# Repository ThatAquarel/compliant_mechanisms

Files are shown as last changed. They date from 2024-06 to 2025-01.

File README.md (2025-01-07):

# Bending Robotic Arm

Built on compliant mechanisms, and handed shearing auxetics. Achieved a snake-like, organic movement. An optical positioning feedback loop completes the control system. The hardware interface is governed by Arduino.

Icons

### Achieved Flexibility
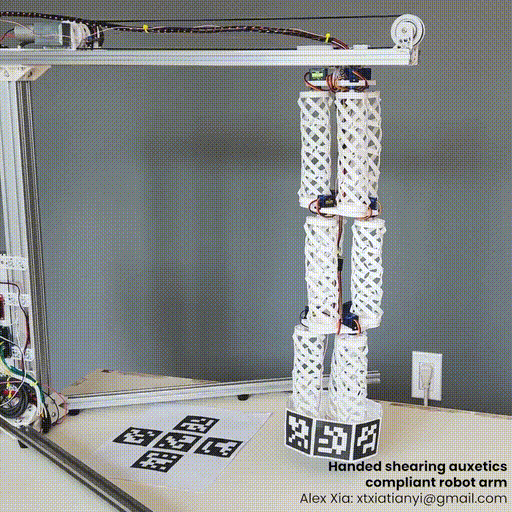
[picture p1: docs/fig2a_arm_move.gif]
Arm Bending Move


### Movement Range
Arm Movement Range

## Author

Alex Xia, personal project. June-December 2024.

## Mechanism of Action

3D-printed, flexible muscles arrayed in sets of three, and stacked together allow for the movement range of the robotic arm. Parallelogram lattices are mapped onto the side surface of a cylinder of ID `38.4mm`. An axial twisting torque extends and contracts the muscle.

### Single Muscle Extension and Contraction

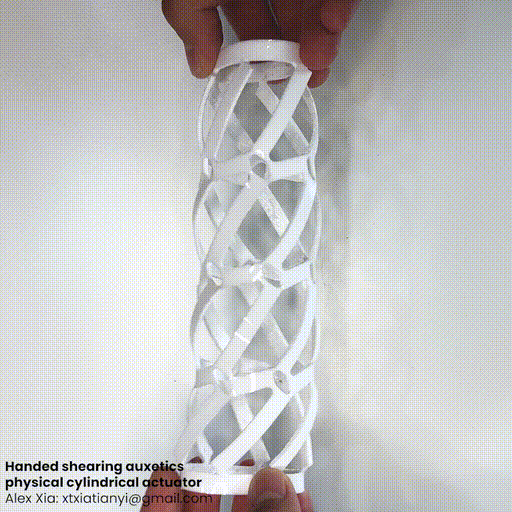
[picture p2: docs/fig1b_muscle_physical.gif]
Muscle Extension and Contraction by Hand


### Muscle Simulation, Blender
Muscle Simulation

## The Concept

Unlike traditional robotic arms, which pivot rigidly around bearings, the compliant muscles allow this arm to bend and twist upon itself, making this special, in my eyes. The snake-like organic movements contrast with the elbowing motion of assembly-line robots, for instance. 

The soft plastics of which the muscles are composed grant safety and simplicity to the design: there are no heavy metal parts moving – which eases assembly – and few differing components (only light servo motors, wiring, and plastic parts).

I see further iterations of this prototype interacting with humans, in palliative care, for example, and for microscopic manipulation.

## How it Works

3D-printed, flexible, cylindrical muscles which contract and extend upon an axial twisting force are arrayed in sets of three, and then layered – achieving a smooth, flexing motion of the whole structure: a flexible and compliant robotic arm.

Each muscle consists of a matrix of parallelograms – which can be sheared into rectangles, achieving extension – mapped and curved onto the surface of a cylinder. 

9 servo motors individually apply torque on each of the muscles to attain a specific pose, which the target is confirmed by an optical positioning system (see Project 2).

This visual positioning data, indeed, completes the feedback loop. A Python script minimizes the distance between the achieved and desired pose, and relays the motor positions to the hardware-controlling Arduino using serial communication. The achieved kinematics resemble that of three stacked Stewart platforms.

## Codebase

- `shearing_auxetics/`: Auxetic materials research and prototypes of muscles
    - `openscad/`: V1: Mesh generation with OpenSCAD.
    - `blender/`: V2: Mesh generation with Python and Blender - final working version of muscles.
    - `render/`: Rendering of V2.
    - `simulation/`: Simulation of edges of V2.

- `arm/`: Implementation of shearing auxetics for the bending arm
    - `hardware/arm_interface`: Serial interface between computer and hardware with Arduino on PlatformIO 
    - `software/`: Control loop on Python
        - `drafts/`: Python control of robotic arm with GUI
            - `optical_positioning_optimize_center.py`: Nelder-mead optimisation to arm position.
            - `optical_positioning_optimize_center_manual.py`: Manual slider-control of robotic arm.
        - `mit/`: Interpolated move examples for MIT Maker Portfolio from recorded positions.

- `optical_positioning/`: Optical positioning for motion tracking and control loop feedback
    - `optical_positioning/`: Optical positioning Python package root.
    - `b_calibrate/`: Cached calibration images.
    - `c_calibrate_matrix/`: Cached calibration matrices.
    - `drafts/`: Testing code for iterative developement.

## Contact

- [Tian Yi, "Alex", Xia](https://github.com/ThatAquarel), xtxiatianyi@gmail.com: 

## References

- Compliant Mechanisms (Howell, 2001).
- Handedness in Shearing Auxetics Creates Rigid and Compliant Structures (Lipton et al., 2018).

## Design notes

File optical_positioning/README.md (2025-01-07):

# Optical Positioning System

Three fisheye cameras locate ArUco markers within their field of view, and transform their perspectives into 3D positions.

Icons

### Custom 3D Motion Capture Software

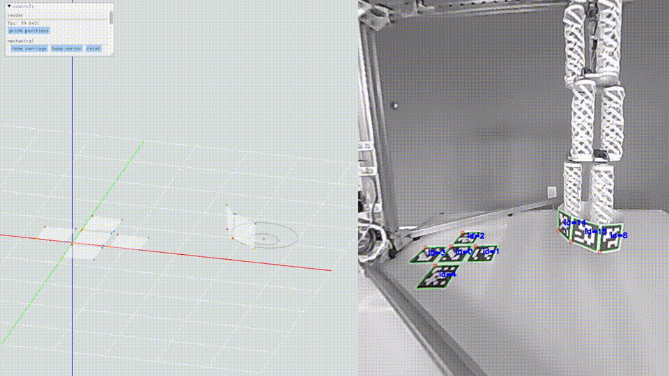
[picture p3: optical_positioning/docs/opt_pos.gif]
3D Motion Capture


### Marker Tracking

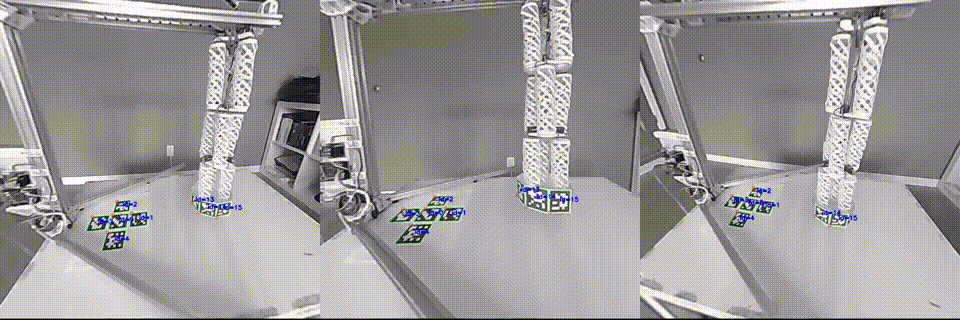
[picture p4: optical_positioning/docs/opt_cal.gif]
ArUco Marker Capture


### Camera Views

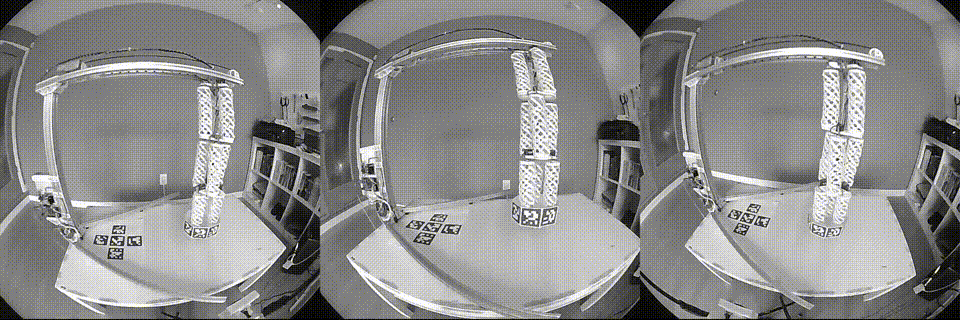
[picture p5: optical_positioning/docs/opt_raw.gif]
Fisheye Camera Views


## Author

Alex Xia, personal project. June-December 2024.

## Computer Vision Principles

The 3D-printed mounts for each of the cameras is my own design. The optical positioning pipeline, along with the feedback loop for my robotic arm, is also my own work built on open-source packages. OpenCV handled the ArUco marker generation and detection, and provided helper functions for calibrating the cameras, and solving for perspective, for example. However, making these preexisting tools work together reliably and fast was my responsibility. Most notably, the linear algebra to match the perspectives of the cameras to each other (the bulk of the computation) is my work, as optimizing my code for up to 120 frames per second required multithreading math.

The theory that backed this implementation was found in research papers and online articles which detailed the Perspective-n-Point problem, and OpenCV’s documentation. Dr. Anton's "Elementary Linear Algebra" also came in handy.

## Design Goals

In building my flexible robotic arm, I realized I needed a reliable positioning system for feedback. I knew that optical was the way to go, but due to the high price point of commercial options, I built my own for cheap, open-sourced it – all while serving as a learning experience for math. 

Currently, the cameras are fixed in place, while objects within their fields of view move: perfect for motion capture in robotics. A similar algorithm holds true if the cameras move, instead, which is my next goal. The cameras can then be placed on the end effector (or achieve the same perspective by the mediation of fiber optic cables) – a necessary field of view if we’re talking about surgery: a possible application for miniaturized flexible robotic arms. This extension of my positioning system is my current goal.

## How it Works

After researching the extravagant pricing options of OptiTrack, I bought three USB fisheye cameras with a 180deg lens for around 100$, and 3D-printed mounts to bolt onto cymbal stands I borrowed from my drum set.

I first calibrated each of the cameras, acquiring their projection and distortion matrices, with different pictures of a known-size checkerboard pattern. The image distorted by the fisheye lens can be undistorted using these matrices, making lines appear straight in-frame. This is crucial as the ArUco marker corner detection would not work otherwise.

Using a known cross pattern, I computed the relative transformation matrices between each camera using OpenCV’s Perspective-n-Point solver. The absolute position with respect to the cross pattern can be therefore determined for each subsequent marker that appears in at least two of the cameras.

## Requirements

- glfw==2.7.0
- imgui==2.0.0
- matplotlib==3.10.0
- numpy==2.2.1
- opencv_python==4.10.0.84
- PyOpenGL==3.1.7
- PyOpenGL==3.1.7
- scipy==1.15.0
- setuptools==69.5.1

## Codebase

- `optical_positioning/`: Optical positioning for motion tracking and control loop feedback
    - `optical_positioning/`: Optical positioning Python package root.
        - `a_constants.py`: Program constants: number of cameras, reference frame ArUco marker placements.
        - `b_calibrate.py`: Take calibration pictures.
        - `c_calibrate_matrix.py`: Fisheye camera calibration and distortion matrix acquisition.
        - `d_compute_pose.py`: 3D pose computation of detected markers from 3 perspectives.
        - `e_render.py`: OpenGL-based custom rendering engine for motion tracking.

    - `b_calibrate/`: Cached calibration images.
    - `c_calibrate_matrix/`: Cached calibration matrices.
    - `drafts/`: Testing code for iterative developement.

## Contact

- [Tian Yi, "Alex", Xia](https://github.com/ThatAquarel), xtxiatianyi@gmail.com:

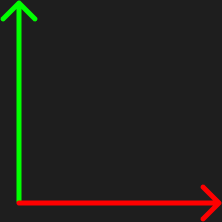
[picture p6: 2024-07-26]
optical_positioning/drafts/aruco/xy_arrows.png

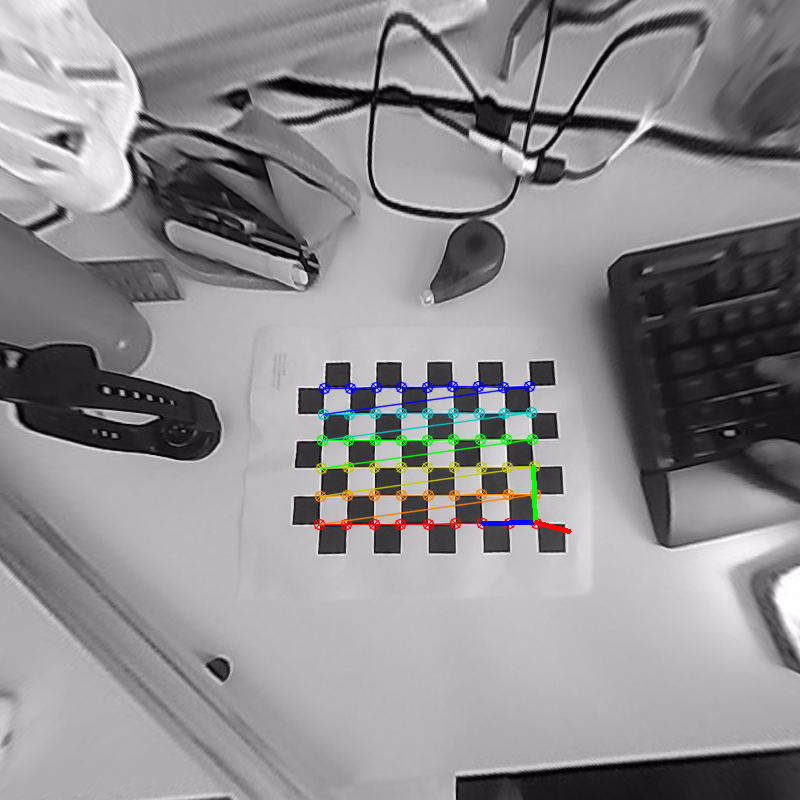
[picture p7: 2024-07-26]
optical_positioning/drafts/raw_compute/img_1_pose.png

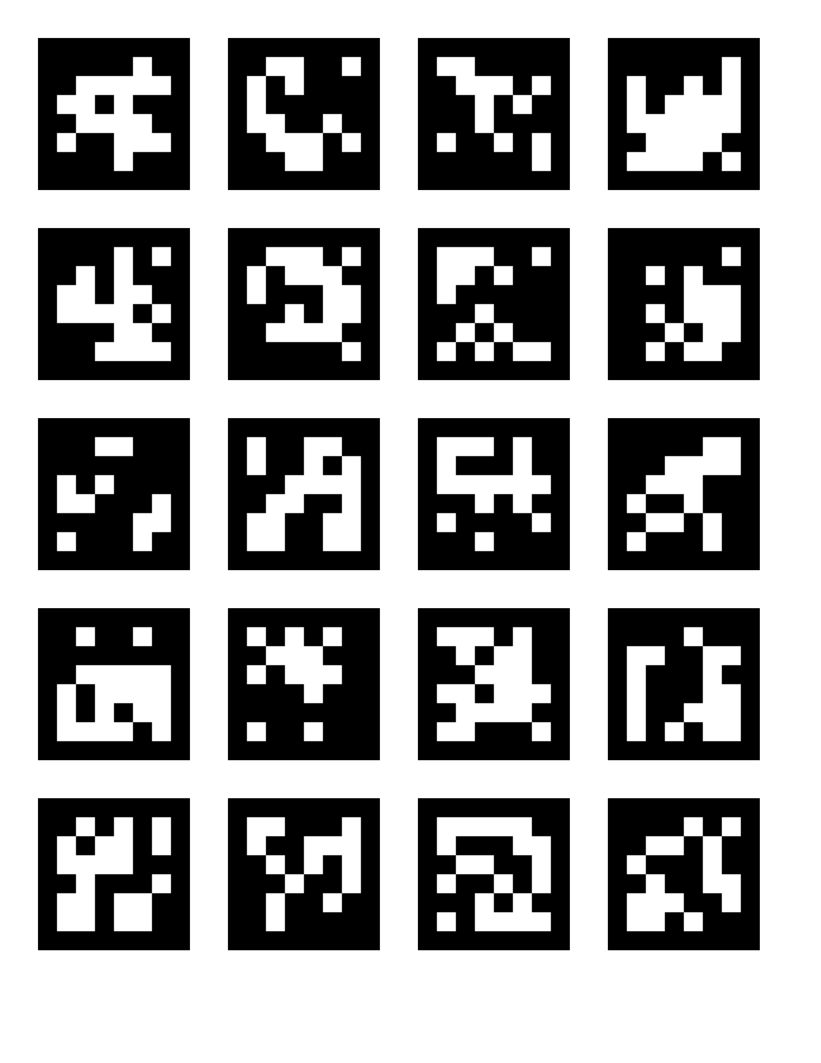
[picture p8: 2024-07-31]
optical_positioning/drafts/aruco/generate_ngrid_4cm.png

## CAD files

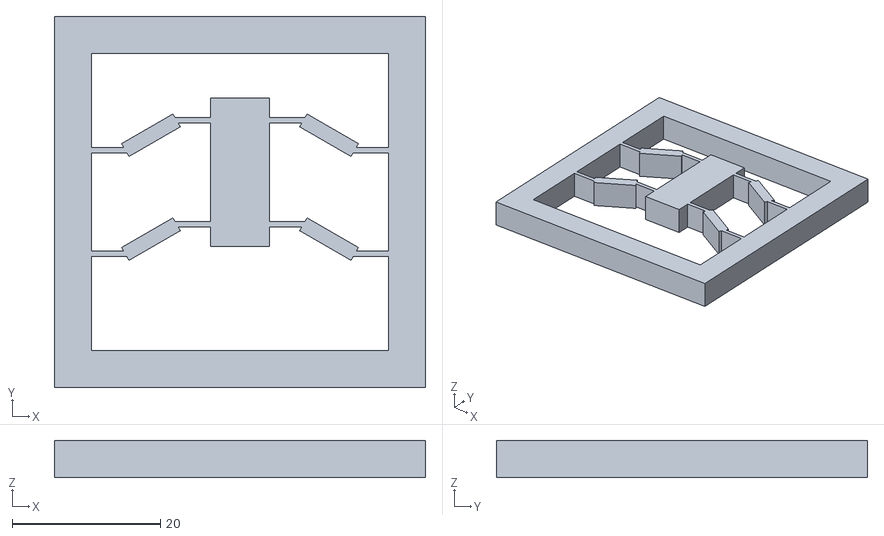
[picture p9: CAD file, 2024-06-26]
bistable.stl
50.0 x 50.0 x 5.00

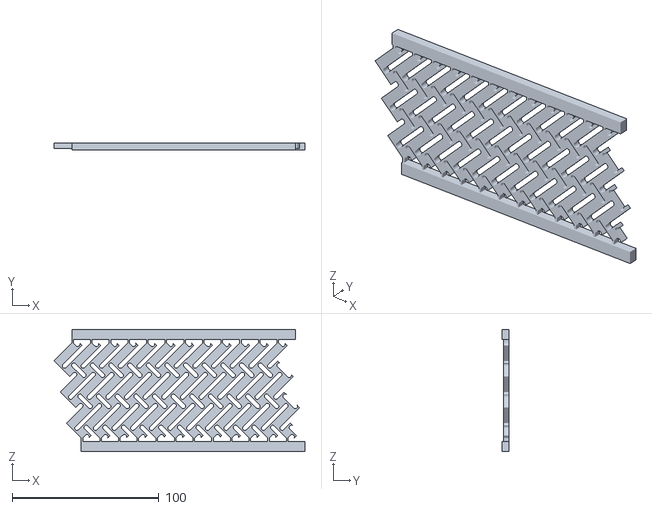
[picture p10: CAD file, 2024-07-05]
shearing_auxetics/blender/prototyping/flat_asymmetric_ratio_n_v4.stl
171.3 x 5.00 x 83.6

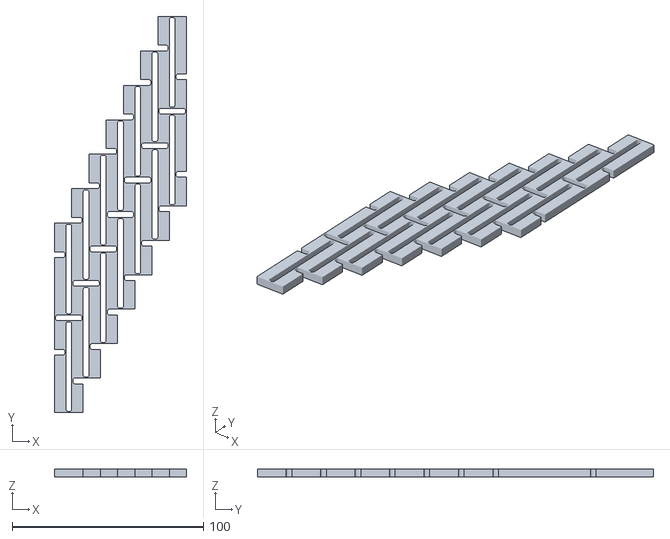
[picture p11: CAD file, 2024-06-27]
shearing_auxetics/openscad/flat_asymmetric_ratio_2_8_5.stl
69.0 x 207.0 x 4.00

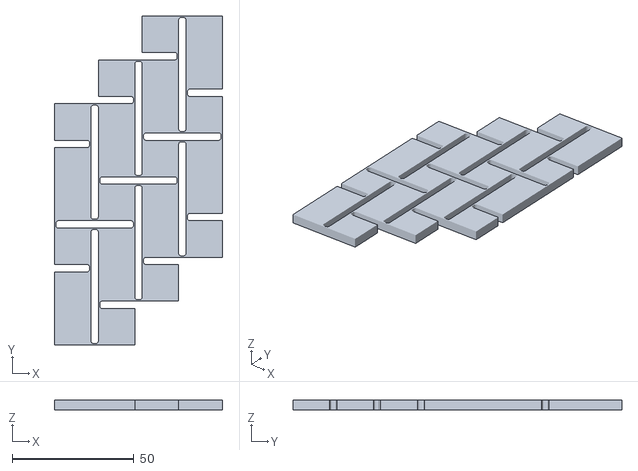
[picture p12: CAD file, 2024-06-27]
shearing_auxetics/openscad/flat_asymmetric_ratio_2.stl
69.0 x 135.0 x 4.00

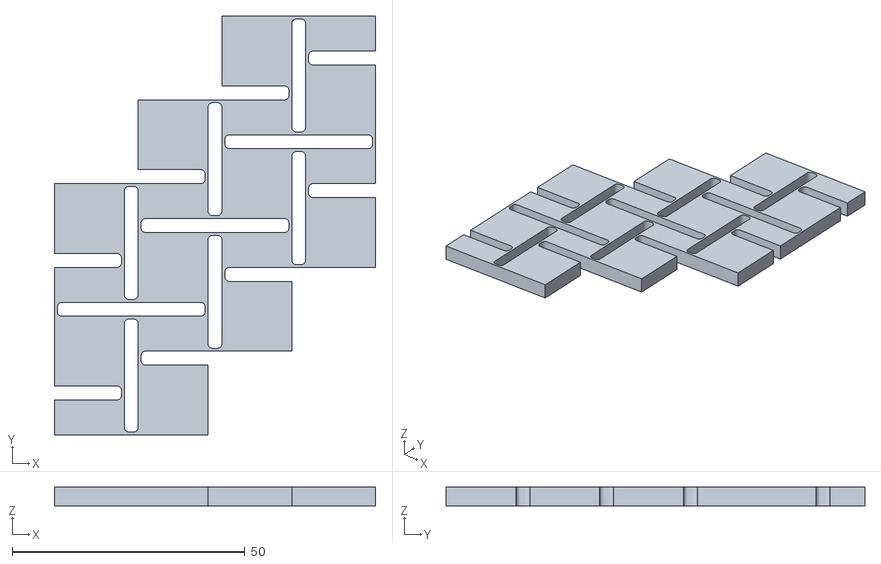
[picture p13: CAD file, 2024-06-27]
shearing_auxetics/openscad/flat_asymmetric_ratio_0.5.stl
69.0 x 90.0 x 4.00

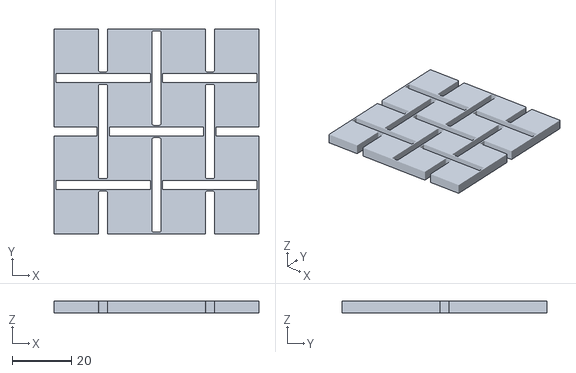
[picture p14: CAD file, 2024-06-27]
shearing_auxetics/openscad/flat_ratio_equal.stl
69.0 x 69.0 x 4.00

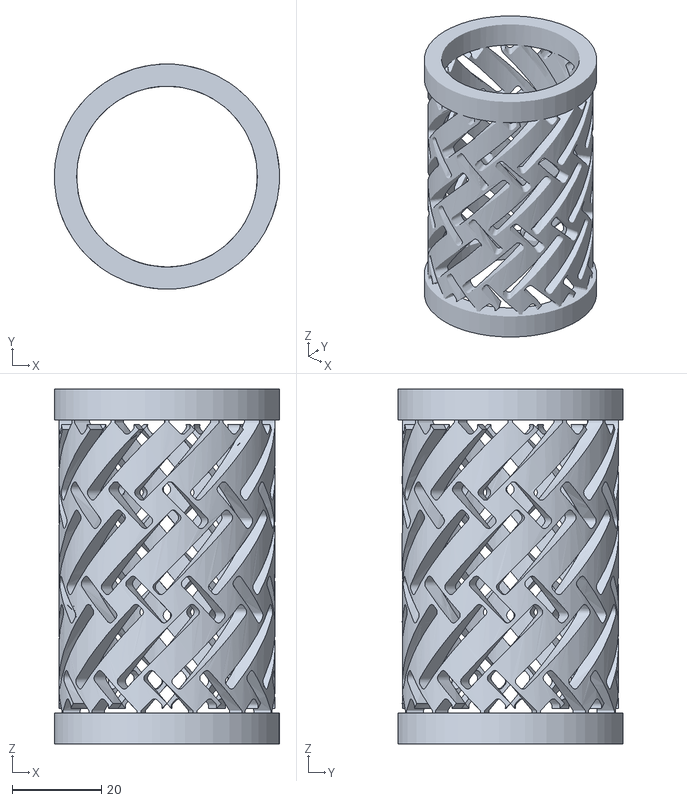
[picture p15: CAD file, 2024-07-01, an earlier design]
shearing_auxetics/blender/prototyping/flat_asymmetric_ratio_n_v2.stl
50.6 x 50.6 x 79.8

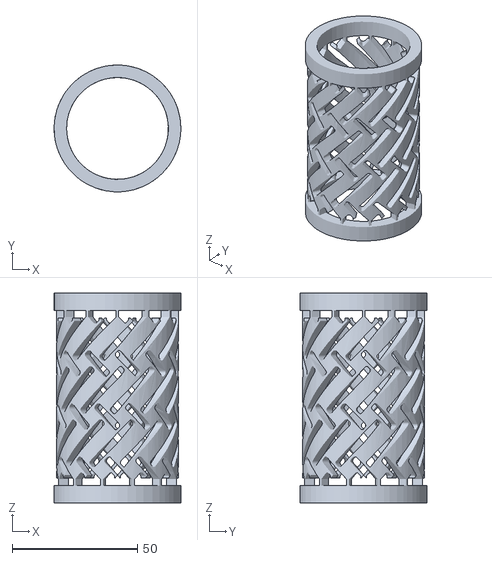
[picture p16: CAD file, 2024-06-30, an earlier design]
shearing_auxetics/blender/prototyping/flat_asymmetric_ratio_n_v1.stl
50.6 x 50.6 x 83.8

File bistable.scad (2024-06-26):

difference(){
    cube([50, 50, 5], true);
    cube([40, 40, 10], true);
}

translate([0,4,0]) {
    intersection() {
            cube([18, 20, 10], true);
    union() {
        cube([8, 20, 5], true);
        translate([0, -7, 0]) cube([50,0.75,5], true);
        translate([0, +7, 0]) cube([50,0.75,5], true);
    }
}
};


difference() {
    union(){
        translate([0, -7, 0]) cube([50,0.75,5], true);
        translate([0, +7, 0]) cube([50,0.75,5], true);
    }

    cube([30,30,8], true);
}


translate([12,9,0]) rotate([0,0,-30]) cube([8, 2, 5], true);

translate([-12,9,0]) rotate([0,0,30]) cube([8, 2, 5], true);

translate([12,-5,0]) rotate([0,0,-30]) cube([8, 2, 5], true);

translate([-12,-5,0]) rotate([0,0,30]) cube([8, 2, 5], true);

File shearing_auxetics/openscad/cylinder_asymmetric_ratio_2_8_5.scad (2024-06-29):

// Generated by SolidPython 1.1.3 on 2024-06-28 17:05:18
$fn=32;


difference() {
	cylinder(h = 58.13776741499453, r = 25.623451563018378);
	cylinder(h = 58.13776741499453, r = 21.623451563018378);
	translate(v = [0, 0, 6.037383539249432]) {
		rotate(a = [0, 0, -10.5]) {
			rotate(a = [26.56505117707799, 0, 0]) {
				rotate(a = [0, 90, 0]) {
					linear_extrude(height = 25.623451563018378) {
						offset(r = 1) {
							translate(v = [-5.9000000000, -0.5000000000]) {
								square(size = [11.8000000000, 1]);
							}
						}
					}
				}
			}
		}
	}
	translate(v = [0, 0, 6.037383539249432]) {
		rotate(a = [0, 0, 34.49999999999999]) {
			rotate(a = [26.56505117707799, 0, 0]) {
				rotate(a = [0, 90, 0]) {
					linear_extrude(height = 25.623451563018378) {
						offset(r = 1) {
							translate(v = [-5.9000000000, -0.5000000000]) {
								square(size = [11.8000000000, 1]);
							}
						}
					}
				}
			}
		}
	}
	translate(v = [0, 0, 6.037383539249432]) {
		rotate(a = [0, 0, 79.5]) {
			rotate(a = [26.56505117707799, 0, 0]) {
				rotate(a = [0, 90, 0]) {
					linear_extrude(height = 25.623451563018378) {
						offset(r = 1) {
							translate(v = [-5.9000000000, -0.5000000000]) {
								square(size = [11.8000000000, 1]);
							}
						}
					}
				}
			}
		}
	}
	translate(v = [0, 0, 6.037383539249432]) {
		rotate(a = [0, 0, 124.5]) {
			rotate(a = [26.56505117707799, 0, 0]) {
				rotate(a = [0, 90, 0]) {
					linear_extrude(height = 25.623451563018378) {
						offset(r = 1) {
							translate(v = [-5.9000000000, -0.5000000000]) {
								square(size = [11.8000000000, 1]);
							}
						}
					}
				}
			}
		}
	}
	translate(v = [0, 0, 6.037383539249432]) {
		rotate(a = [0, 0, 169.5]) {
			rotate(a = [26.56505117707799, 0, 0]) {
				rotate(a = [0, 90, 0]) {
					linear_extrude(height = 25.623451563018378) {
						offset(r = 1) {
							translate(v = [-5.9000000000, -0.5000000000]) {
								square(size = [11.8000000000, 1]);
							}
						}
					}
				}
			}
		}
	}
	translate(v = [0, 0, 6.037383539249432]) {
		rotate(a = [0, 0, 214.49999999999997]) {
			rotate(a = [26.56505117707799, 0, 0]) {
				rotate(a = [0, 90, 0]) {
					linear_extrude(height = 25.623451563018378) {
						offset(r = 1) {
							translate(v = [-5.9000000000, -0.5000000000]) {
								square(size = [11.8000000000, 1]);
							}
						}
					}
				}
			}
		}
	}
	translate(v = [0, 0, 6.037383539249432]) {
		rotate(a = [0, 0, 259.5]) {
			rotate(a = [26.56505117707799, 0, 0]) {
				rotate(a = [0, 90, 0]) {
					linear_extrude(height = 25.623451563018378) {
						offset(r = 1) {
							translate(v = [-5.9000000000, -0.5000000000]) {
								square(size = [11.8000000000, 1]);
							}
						}
					}
				}
			}
		}
	}
	translate(v = [0, 0, 6.037383539249432]) {
		rotate(a = [0, 0, 304.5]) {
			rotate(a = [26.56505117707799, 0, 0]) {
				rotate(a = [0, 90, 0]) {
					linear_extrude(height = 25.623451563018378) {
						offset(r = 1) {
							translate(v = [-5.9000000000, -0.5000000000]) {
								square(size = [11.8000000000, 1]);
							}
						}
					}
				}
			}
		}
	}
	translate(v = [0, 0, 17.44133022449836]) {
		rotate(a = [0, 0, 40.49999999999999]) {
			rotate(a = [-63.43494882292201, 0, 0]) {
				rotate(a = [0, 90, 0]) {
					linear_extrude(height = 25.623451563018378) {
						offset(r = 1) {
							translate(v = [-15.9000000000, -0.5000000000]) {
								square(size = [31.8000000000, 1]);
							}
						}
					}
				}
			}
		}
	}
	translate(v = [0, 0, 17.44133022449836]) {
		rotate(a = [0, 0, 85.5]) {
			rotate(a = [-63.43494882292201, 0, 0]) {
				rotate(a = [0, 90, 0]) {
					linear_extrude(height = 25.623451563018378) {
						offset(r = 1) {
							translate(v = [-15.9000000000, -0.5000000000]) {
								square(size = [31.8000000000, 1]);
							}
						}
					}
				}
			}
		}
	}
	translate(v = [0, 0, 17.44133022449836]) {
		rotate(a = [0, 0, 130.5]) {
			rotate(a = [-63.43494882292201, 0, 0]) {
				rotate(a = [0, 90, 0]) {
					linear_extrude(height = 25.623451563018378) {
						offset(r = 1) {
							translate(v = [-15.9000000000, -0.5000000000]) {
								square(size = [31.8000000000, 1]);
							}
						}
					}
				}
			}
		}
	}
	translate(v = [0, 0, 17.44133022449836]) {
		rotate(a = [0, 0, 175.5]) {
			rotate(a = [-63.43494882292201, 0, 0]) {
				rotate(a = [0, 90, 0]) {
					linear_extrude(height = 25.623451563018378) {
						offset(r = 1) {
							translate(v = [-15.9000000000, -0.5000000000]) {
								square(size = [31.8000000000, 1]);
							}
						}
					}
				}
			}
		}
	}
	translate(v = [0, 0, 17.44133022449836]) {
		rotate(a = [0, 0, 220.5]) {
			rotate(a = [-63.43494882292201, 0, 0]) {
				rotate(a = [0, 90, 0]) {
					linear_extrude(height = 25.623451563018378) {
						offset(r = 1) {
							translate(v = [-15.9000000000, -0.5000000000]) {
								square(size = [31.8000000000, 1]);
							}
						}
					}
				}
			}
		}
	}
	translate(v = [0, 0, 17.44133022449836]) {
		rotate(a = [0, 0, 265.5]) {
			rotate(a = [-63.43494882292201, 0, 0]) {
				rotate(a = [0, 90, 0]) {
					linear_extrude(height = 25.623451563018378) {
						offset(r = 1) {
							translate(v = [-15.9000000000, -0.5000000000]) {
								square(size = [31.8000000000, 1]);
							}
						}
					}
				}
			}
		}
	}
	translate(v = [0, 0, 17.44133022449836]) {
		rotate(a = [0, 0, 310.5]) {
			rotate(a = [-63.43494882292201, 0, 0]) {
				rotate(a = [0, 90, 0]) {
					linear_extrude(height = 25.623451563018378) {
						offset(r = 1) {
							translate(v = [-15.9000000000, -0.5000000000]) {
								square(size = [31.8000000000, 1]);
							}
						}
					}
				}
			}
		}
	}
	translate(v = [0, 0, 17.44133022449836]) {
		rotate(a = [0, 0, 355.49999999999994]) {
			rotate(a = [-63.43494882292201, 0, 0]) {
				rotate(a = [0, 90, 0]) {
					linear_extrude(height = 25.623451563018378) {
						offset(r = 1) {
							translate(v = [-15.9000000000, -0.5000000000]) {
								square(size = [31.8000000000, 1]);
							}
						}
					}
				}
			}
		}
	}
	translate(v = [0, 0, 21.037383539249433]) {
		rotate(a = [0, 0, -10.5]) {
			rotate(a = [26.56505117707799, 0, 0]) {
				rotate(a = [0, 90, 0]) {
					linear_extrude(height = 25.623451563018378) {
						offset(r = 1) {
							translate(v = [-5.9000000000, -0.5000000000]) {
								square(size = [11.8000000000, 1]);
							}
						}
					}
				}
			}
		}
	}
	translate(v = [0, 0, 21.037383539249433]) {
		rotate(a = [0, 0, 34.49999999999999]) {
			rotate(a = [26.56505117707799, 0, 0]) {
				rotate(a = [0, 90, 0]) {
					linear_extrude(height = 25.623451563018378) {
						offset(r = 1) {
							translate(v = [-5.9000000000, -0.5000000000]) {
								square(size = [11.8000000000, 1]);
							}
						}
					}
				}
			}
		}
	}
	translate(v = [0, 0, 21.037383539249433]) {
		rotate(a = [0, 0, 79.5]) {
			rotate(a = [26.56505117707799, 0, 0]) {
				rotate(a = [0, 90, 0]) {
					linear_extrude(height = 25.623451563018378) {
						offset(r = 1) {
							translate(v = [-5.9000000000, -0.5000000000]) {
								square(size = [11.8000000000, 1]);
							}
						}
					}
				}
			}
		}
	}
	translate(v = [0, 0, 21.037383539249433]) {
		rotate(a = [0, 0, 124.5]) {
			rotate(a = [26.56505117707799, 0, 0]) {
				rotate(a = [0, 90, 0]) {
					linear_extrude(height = 25.623451563018378) {
						offset(r = 1) {
							translate(v = [-5.9000000000, -0.5000000000]) {
								square(size = [11.8000000000, 1]);
							}
						}
					}
				}
			}
		}
	}
	translate(v = [0, 0, 21.037383539249433]) {
		rotate(a = [0, 0, 169.5]) {
			rotate(a = [26.56505117707799, 0, 0]) {
				rotate(a = [0, 90, 0]) {
					linear_extrude(height = 25.623451563018378) {
						offset(r = 1) {
							translate(v = [-5.9000000000, -0.5000000000]) {
								square(size = [11.8000000000, 1]);
							}
						}
					}
				}
			}
		}
	}
	translate(v = [0, 0, 21.037383539249433]) {
		rotate(a = [0, 0, 214.49999999999997]) {
			rotate(a = [26.56505117707799, 0, 0]) {
				rotate(a = [0, 90, 0]) {
					linear_extrude(height = 25.623451563018378) {
						offset(r = 1) {
							translate(v = [-5.9000000000, -0.5000000000]) {
								square(size = [11.8000000000, 1]);
							}
						}
					}
				}
			}
		}
	}
	translate(v = [0, 0, 21.037383539249433]) {
		rotate(a = [0, 0, 259.5]) {
			rotate(a = [26.56505117707799, 0, 0]) {
				rotate(a = [0, 90, 0]) {
					linear_extrude(height = 25.623451563018378) {
						offset(r = 1) {
							translate(v = [-5.9000000000, -0.5000000000]) {
								square(size = [11.8000000000, 1]);
							}
						}
					}
				}
			}
		}
	}
	translate(v = [0, 0, 21.037383539249433]) {
		rotate(a = [0, 0, 304.5]) {
			rotate(a = [26.56505117707799, 0, 0]) {
				rotate(a = [0, 90, 0]) {
					linear_extrude(height = 25.623451563018378) {
						offset(r = 1) {
							translate(v = [-5.9000000000, -0.5000000000]) {
								square(size = [11.8000000000, 1]);
							}
						}
					}
				}
			}
		}
	}
	translate(v = [0, 0, 32.44133022449836]) {
		rotate(a = [0, 0, 40.49999999999999]) {
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

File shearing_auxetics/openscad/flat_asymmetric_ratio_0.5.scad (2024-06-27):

// Generated by SolidPython 1.1.3 on 2024-06-27 12:35:24
$fn=32;


translate(v = [0, -18, 0]) {
	intersection() {
		union() {
			cube(size = 0);
			translate(v = [0.0, 0.0, 0]) {
				cube(size = [15, 15, 4]);
			}
			translate(v = [0.6, 15.0, 0]) {
				rotate(a = [0, 0, 90]) {
					union() {
						cube(size = [3, 0.6000000000, 4]);
						translate(v = [1, -1, 0]) {
							mirror(v = [1, 0, 0]) {
								difference() {
									cube(size = [1, 1, 4]);
									cylinder(h = 4, r = 1);
								}
							}
						}
						translate(v = [2, -1, 0]) {
							difference() {
								cube(size = [1, 1, 4]);
								cylinder(h = 4, r = 1);
							}
						}
					}
				}
			}
			translate(v = [0.0, 0.6, 0]) {
				rotate(a = [0, 0, 180]) {
					union() {
						cube(size = [3, 0.6000000000, 4]);
						translate(v = [1, -1, 0]) {
							mirror(v = [1, 0, 0]) {
								difference() {
									cube(size = [1, 1, 4]);
									cylinder(h = 4, r = 1);
								}
							}
						}
						translate(v = [2, -1, 0]) {
							difference() {
								cube(size = [1, 1, 4]);
								cylinder(h = 4, r = 1);
							}
						}
					}
				}
			}
			translate(v = [18.0, 18.0, 0]) {
				cube(size = [15, 15, 4]);
			}
			translate(v = [18.6, 33.0, 0]) {
				rotate(a = [0, 0, 90]) {
					union() {
						cube(size = [3, 0.6000000000, 4]);
						translate(v = [1, -1, 0]) {
							mirror(v = [1, 0, 0]) {
								difference() {
									cube(size = [1, 1, 4]);
									cylinder(h = 4, r = 1);
								}
							}
						}
						translate(v = [2, -1, 0]) {
							difference() {
								cube(size = [1, 1, 4]);
								cylinder(h = 4, r = 1);
							}
						}
					}
				}
			}
			translate(v = [18.0, 18.6, 0]) {
				rotate(a = [0, 0, 180]) {
					union() {
						cube(size = [3, 0.6000000000, 4]);
						translate(v = [1, -1, 0]) {
							mirror(v = [1, 0, 0]) {
								difference() {
									cube(size = [1, 1, 4]);
									cylinder(h = 4, r = 1);
								}
							}
						}
						translate(v = [2, -1, 0]) {
							difference() {
								cube(size = [1, 1, 4]);
								cylinder(h = 4, r = 1);
							}
						}
					}
				}
			}
			translate(v = [36.0, 36.0, 0]) {
				cube(size = [15, 15, 4]);
			}
			translate(v = [36.6, 51.0, 0]) {
				rotate(a = [0, 0, 90]) {
					union() {
						cube(size = [3, 0.6000000000, 4]);
						translate(v = [1, -1, 0]) {
							mirror(v = [1, 0, 0]) {
								difference() {
									cube(size = [1, 1, 4]);
									cylinder(h = 4, r = 1);
								}
							}
						}
						translate(v = [2, -1, 0]) {
							difference() {
								cube(size = [1, 1, 4]);
								cylinder(h = 4, r = 1);
							}
						}
					}
				}
			}
			translate(v = [36.0, 36.6, 0]) {
				rotate(a = [0, 0, 180]) {
					union() {
						cube(size = [3, 0.6000000000, 4]);
						translate(v = [1, -1, 0]) {
							mirror(v = [1, 0, 0]) {
								difference() {
									cube(size = [1, 1, 4]);
									cylinder(h = 4, r = 1);
								}
							}
						}
						translate(v = [2, -1, 0]) {
							difference() {
								cube(size = [1, 1, 4]);
								cylinder(h = 4, r = 1);
							}
						}
					}
				}
			}
			translate(v = [54.0, 54.0, 0]) {
				cube(size = [15, 15, 4]);
			}
			translate(v = [54.6, 69.0, 0]) {
				rotate(a = [0, 0, 90]) {
					union() {
						cube(size = [3, 0.6000000000, 4]);
						translate(v = [1, -1, 0]) {
							mirror(v = [1, 0, 0]) {
								difference() {
									cube(size = [1, 1, 4]);
									cylinder(h = 4, r = 1);
								}
							}
						}
						translate(v = [2, -1, 0]) {
							difference() {
								cube(size = [1, 1, 4]);
								cylinder(h = 4, r = 1);
							}
						}
					}
				}
			}
			translate(v = [54.0, 54.6, 0]) {
				rotate(a = [0, 0, 180]) {
					union() {
						cube(size = [3, 0.6000000000, 4]);
						translate(v = [1, -1, 0]) {
							mirror(v = [1, 0, 0]) {
								difference() {
									cube(size = [1, 1, 4]);
									cylinder(h = 4, r = 1);
								}
							}
						}
						translate(v = [2, -1, 0]) {
							difference() {
								cube(size = [1, 1, 4]);
								cylinder(h = 4, r = 1);
							}
						}
					}
				}
			}
			translate(v = [0.0, 18.0, 0]) {
				cube(size = [15, 7.5000000000, 4]);
			}
			translate(v = [14.4, 28.5, 0]) {
				rotate(a = [0, 0, 180]) {
					rotate(a = [0, 0, 90]) {
						union() {
							cube(size = [3, 0.6000000000, 4]);
							translate(v = [1, -1, 0]) {
								mirror(v = [1, 0, 0]) {
									difference() {
										cube(size = [1, 1, 4]);
										cylinder(h = 4, r = 1);
									}
								}
							}
							translate(v = [2, -1, 0]) {
								difference() {
									cube(size = [1, 1, 4]);
									cylinder(h = 4, r = 1);
								}
							}
						}
					}
				}
			}
			translate(v = [-3.0, 24.9, 0]) {
				union() {
					cube(size = [3, 0.6000000000, 4]);
					translate(v = [1, -1, 0]) {
						mirror(v = [1, 0, 0]) {
							difference() {
								cube(size = [1, 1, 4]);
								cylinder(h = 4, r = 1);
							}
						}
					}
					translate(v = [2, -1, 0]) {
						difference() {
							cube(size = [1, 1, 4]);
							cylinder(h = 4, r = 1);
						}
					}
				}
			}
			translate(v = [18.0, 36.0, 0]) {
				cube(size = [15, 7.5000000000, 4]);
			}
			translate(v = [32.4, 46.5, 0]) {
				rotate(a = [0, 0, 180]) {
					rotate(a = [0, 0, 90]) {
						union() {
							cube(size = [3, 0.6000000000, 4]);
							translate(v = [1, -1, 0]) {
								mirror(v = [1, 0, 0]) {
									difference() {
										cube(size = [1, 1, 4]);
										cylinder(h = 4, r = 1);
									}
								}
							}
							translate(v = [2, -1, 0]) {
								difference() {
									cube(size = [1, 1, 4]);
									cylinder(h = 4, r = 1);
								}
							}
						}
					}
				}
			}
			translate(v = [15.0, 42.9, 0]) {
				union() {
					cube(size = [3, 0.6000000000, 4]);
					translate(v = [1, -1, 0]) {
						mirror(v = [1, 0, 0]) {
							difference() {
								cube(size = [1, 1, 4]);
								cylinder(h = 4, r = 1);
							}
						}
					}
					translate(v = [2, -1, 0]) {
						difference() {
							cube(size = [1, 1, 4]);
							cylinder(h = 4, r = 1);
						}
					}
				}
			}
			translate(v = [36.0, 54.0, 0]) {
				cube(size = [15, 7.5000000000, 4]);
			}
			translate(v = [50.4, 64.5, 0]) {
				rotate(a = [0, 0, 180]) {
					rotate(a = [0, 0, 90]) {
						union() {
							cube(size = [3, 0.6000000000, 4]);
							translate(v = [1, -1, 0]) {
								mirror(v = [1, 0, 0]) {
									difference() {
										cube(size = [1, 1, 4]);
										cylinder(h = 4, r = 1);
									}
								}
							}
							translate(v = [2, -1, 0]) {
								difference() {
									cube(size = [1, 1, 4]);
									cylinder(h = 4, r = 1);
								}
							}
						}
					}
				}
			}
			translate(v = [33.0, 60.9, 0]) {
				union() {
					cube(size = [3, 0.6000000000, 4]);
					translate(v = [1, -1, 0]) {
						mirror(v = [1, 0, 0]) {
							difference() {
								cube(size = [1, 1, 4]);
								cylinder(h = 4, r = 1);
							}
						}
					}
					translate(v = [2, -1, 0]) {
						difference() {
							cube(size = [1, 1, 4]);
							cylinder(h = 4, r = 1);
						}
					}
				}
			}
			translate(v = [54.0, 72.0, 0]) {
				cube(size = [15, 7.5000000000, 4]);
			}
			translate(v = [68.4, 82.5, 0]) {
				rotate(a = [0, 0, 180]) {
					rotate(a = [0, 0, 90]) {
						union() {
							cube(size = [3, 0.6000000000, 4]);
							translate(v = [1, -1, 0]) {
								mirror(v = [1, 0, 0]) {
									difference() {
										cube(size = [1, 1, 4]);
										cylinder(h = 4, r = 1);
									}
								}
							}
							translate(v = [2, -1, 0]) {
								difference() {
									cube(size = [1, 1, 4]);
									cylinder(h = 4, r = 1);
								}
							}
						}
					}
				}
			}
			translate(v = [51.0, 78.9, 0]) {
				union() {
					cube(size = [3, 0.6000000000, 4]);
					translate(v = [1, -1, 0]) {
						mirror(v = [1, 0, 0]) {
							difference() {
								cube(size = [1, 1, 4]);
								cylinder(h = 4, r = 1);
							}
						}
					}
					translate(v = [2, -1, 0]) {
						difference() {
							cube(size = [1, 1, 4]);
							cylinder(h = 4, r = 1);
						}
					}
				}
			}
			translate(v = [0.0, 28.5, 0]) {
				cube(size = [15, 15, 4]);
			}
			translate(v = [0.6, 43.5, 0]) {
				rotate(a = [0, 0, 90]) {
					union() {
						cube(size = [3, 0.6000000000, 4]);
						translate(v = [1, -1, 0]) {
							mirror(v = [1, 0, 0]) {
								difference() {
									cube(size = [1, 1, 4]);
									cylinder(h = 4, r = 1);
								}
							}
						}
						translate(v = [2, -1, 0]) {
							difference() {
								cube(size = [1, 1, 4]);
								cylinder(h = 4, r = 1);
							}
						}
					}
				}
			}
			translate(v = [0.0, 29.1, 0]) {
				rotate(a = [0, 0, 180]) {
					union() {
						cube(size = [3, 0.6000000000, 4]);
						translate(v = [1, -1, 0]) {
							mirror(v = [1, 0, 0]) {
								difference() {
									cube(size = [1, 1, 4]);
									cylinder(h = 4, r = 1);
								}
							}
						}
						translate(v = [2, -1, 0]) {
							difference() {
								cube(size = [1, 1, 4]);
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

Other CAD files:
shearing_auxetics/blender/prototyping/flat_asymmetric_ratio_n_v3.stl
shearing_auxetics/openscad/flat_asymmetric_ratio_2.scad
shearing_auxetics/blender/flat_asymmetric_ratio_n.blend
shearing_auxetics/openscad/flat_asymmetric_ratio_2_8_5.scad
shearing_auxetics/openscad/flat_ratio_equal.scad
shearing_auxetics/openscad/linkage.scad

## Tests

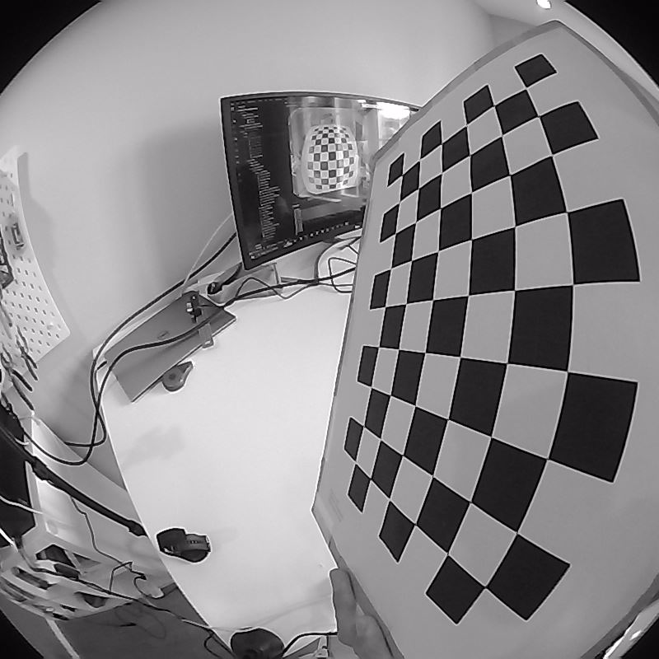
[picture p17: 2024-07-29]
optical_positioning/b_calibrate/cam_1_1.png

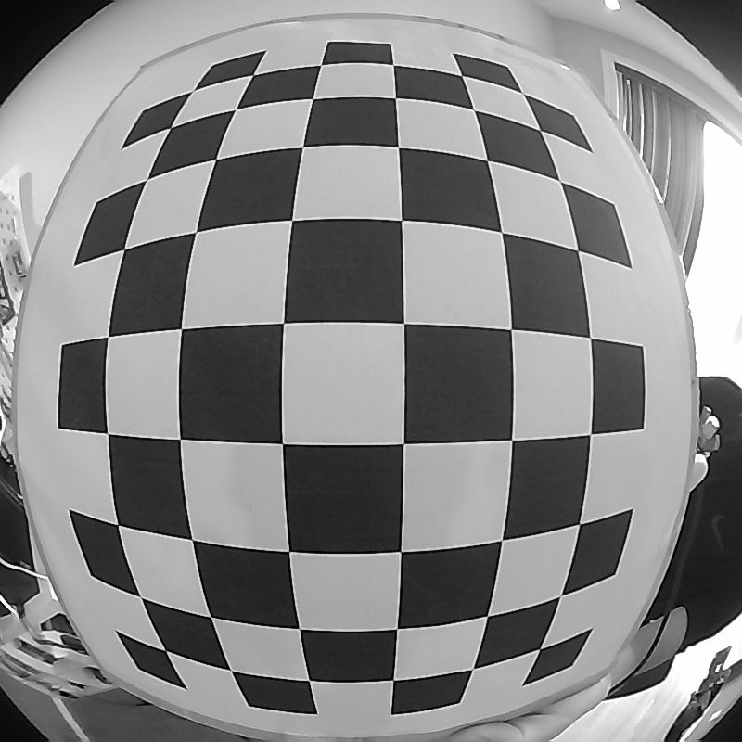
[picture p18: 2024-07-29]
optical_positioning/b_calibrate/cam_1_4.png

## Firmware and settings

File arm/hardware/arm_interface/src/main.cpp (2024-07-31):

#include <Arduino.h>
#include <Servo.h>

// carriage
#define CARRIAGE_INT_PIN 18
#define CARRIAGE_NEG_PIN 2
#define CARRIAGE_POS_PIN 3

#define ENC_A_PIN 19
#define ENC_B_PIN 20
#define ENC_B_PORTD (1 << 1)

#define KP 5.0
#define KI 0.00005
#define KD 0.01

volatile boolean carriage_homing = false;
volatile boolean carriage_ready = false;
volatile float enc_step = 0;
volatile float setpoint = 0;
float prev_dx = 0, integral = 0;
unsigned long prev_t = 0;

// servo
#define N_LAYERS 3
#define N_SIDES 3

#define n_servos (N_LAYERS * N_SIDES)

const int pins[n_servos] = {
    36, 37, 38,
    39, 40, 41,
    42, 43, 45};
const int trim_min[n_servos] = {
    544, 544, 544,
    544, 544, 544,
    544, 544, 544};
const int trim_max[n_servos] = {
    2400, 2400, 2400,
    2400, 2400, 2400,
    2400, 2400, 2400};
const uint8_t home_angle[n_servos] = {
    0,0,0,
    0,0,0,
    0,0,0};

Servo servos[n_servos];
volatile boolean servo_ready = false;
uint8_t servo_setpoint[n_servos];

// serial communications
#define SERIAL_BUFFER_SIZE 64
#define START_FLAG 0x7E
#define END_FLAG 0x7D

#define SYN 0xAB
#define ACK 0x4B
#define NAK 0x5A
#define ERR 0x3C

#define RESET 0x01
#define HOME_CARRIAGE 0x02
#define HOME_SERVO 0x03
#define MOVE_CARRIAGE 0x04
#define MOVE_SERVO 0x05

uint8_t serial_buffer[SERIAL_BUFFER_SIZE];
byte n = 0;
byte packet_status = 0;
uint8_t packet_cmd, packet_len;
boolean new_packet = false;

// prototypes
void enc_isr();
void carriage_reset_isr();
void carriage_motor_set(float value);
void carriage_motor_stop();

void process_pid();
void process_servo();
void process_cmd();

void recv_packet();
void send_packet(uint8_t cmd);

void setup()
{
  pinMode(LED_BUILTIN, OUTPUT);

  // carriage
  // optical homing sensor
  pinMode(CARRIAGE_INT_PIN, INPUT);
  attachInterrupt(digitalPinToInterrupt(CARRIAGE_INT_PIN), carriage_reset_isr, FALLING);

  // rotary encoder
  pinMode(ENC_A_PIN, INPUT_PULLUP);
  attachInterrupt(digitalPinToInterrupt(ENC_A_PIN), enc_isr, RISING);
  pinMode(ENC_B_PIN, INPUT_PULLUP);

  // motor controller
  pinMode(CARRIAGE_NEG_PIN, OUTPUT);
  pinMode(CARRIAGE_POS_PIN, OUTPUT);

  // servos
  for (int i = 0; i < n_servos; i++)
  {
    servos[i].attach(pins[i], trim_min[i], trim_max[i]);
  }

  // serial
  Serial.begin(115200);
}

void enc_isr()
{
  if (PIND & ENC_B_PORTD)
  {
    enc_step++;
  }
  else
  {
    enc_step--;
  }
}

void carriage_reset_isr()
{
  if (!carriage_homing)
  {
    return;
  }
  carriage_motor_stop();
  enc_step = 0;
  setpoint = 0;
  carriage_homing = false;
  carriage_ready = true;
}

void loop()
{
  if (carriage_ready && !carriage_homing)
  {
    process_pid();
  }
  if (servo_ready)
  {
    process_servo();
  }

  recv_packet();
  if (new_packet)
  {
    process_cmd();
    new_packet = false;
  }
}

void process_pid()
{
  unsigned long current_t = micros();
  float dt = (float)(current_t - prev_t) / 1000000.0;
  prev_t = current_t;

  float dx = setpoint - enc_step;
  integral += dx * dt;
  float derivative = (dx - prev_dx) / dt;
  float output = KP * dx + KI * integral + KD * derivative;
  prev_dx = dx;

  carriage_motor_set(output);
}

void carriage_motor_set(float value)
{
  float out = abs(value);
  out = min(out, 255);

  if (out < 15)
  {
    carriage_motor_stop();
    return;
  }

  if (value > 0)
  {
    analogWrite(CARRIAGE_NEG_PIN, 0);
    analogWrite(CARRIAGE_POS_PIN, out);
  }
  else
  {
    analogWrite(CARRIAGE_POS_PIN, 0);
    analogWrite(CARRIAGE_NEG_PIN, out);
  }
}

void carriage_motor_stop()
{
  digitalWrite(CARRIAGE_POS_PIN, 0);
  digitalWrite(CARRIAGE_NEG_PIN, 0);
  // PORTL = PORTL & B11010111;
}

void process_servo()
{
  for (int i = 0; i < n_servos; i++)
  {
    servos[i].write((int)servo_setpoint[i]);
  }
}

void process_cmd()
{
  switch (packet_cmd)
  {
  case SYN:
    send_packet(ACK);
    break;
  case RESET:
    carriage_motor_stop();
    carriage_ready = false;
    carriage_homing = false;

    servo_ready = false;
    send_packet(ACK);
    break;
  case HOME_CARRIAGE:
    if (carriage_homing)
    {
      send_packet(ERR);
      break;
    }
    carriage_homing = true;
    if (digitalRead(CARRIAGE_INT_PIN))
    {
      analogWrite(CARRIAGE_NEG_PIN, 255);
    }
    else
    {
      carriage_reset_isr();
    }
    send_packet(ACK);
    break;
  case HOME_SERVO:
    memcpy((uint8_t *)servo_setpoint, home_angle, n_servos * sizeof(uint8_t));
    servo_ready = true;
    send_packet(ACK);
    break;
  case MOVE_CARRIAGE:
    if (!carriage_ready || carriage_homing)
    {
      send_packet(ERR);
      break;
    }
    if (n != sizeof(setpoint))
    {
      send_packet(NAK);
      break;
    }
    memcpy((float *)&setpoint, serial_buffer, sizeof(setpoint));
    send_packet(ACK);
    break;
  case MOVE_SERVO:
    if (!servo_ready)
    {
      send_packet(ERR);
      break;
    }
    if (n != n_servos * sizeof(uint8_t))
    {
      send_packet(NAK);
      break;
    }
    memcpy((uint8_t *)servo_setpoint, serial_buffer, n_servos * sizeof(uint8_t));
    send_packet(ACK);
    break;
  default:
    send_packet(NAK);
    break;
  }
}

void recv_packet()
{
  // 0: await start flag  uint8
  // 1: command           uint8
  // 2: len               uint8
  // 3: buffer            uint8[len]
  // 4: end flag          uint8

  if (Serial.available() > 1)
  {
    uint8_t rc;
    rc = Serial.read();

    switch (packet_status)
    {
    case 0:
      if (rc == START_FLAG)
      {
        packet_status = 1;
        n = 0;
      }
      break;
    case 1:
      packet_cmd = rc;
      packet_status = 2;
      break;
    case 2:
      packet_len = rc;
      if (packet_len == 0)
      {
        packet_status = 4;
      }
      else
      {
        packet_status = 3;
      }
      break;
    case 3:
      serial_buffer[n] = rc;
      n++;
      if (n >= SERIAL_BUFFER_SIZE)
      {
        n = 0;
      }
      packet_len--;
      if (packet_len == 0)
      {
        packet_status = 4;
      }
      break;
    case 4:
      if (rc == END_FLAG)
      {
        new_packet = true;
      }
      packet_status = 0;
      break;
    }
  }
}

void send_packet(uint8_t cmd)
{
  Serial.write(0x00);
  Serial.write(START_FLAG);
  Serial.write(cmd);
  Serial.write((uint8_t)0x00);
  Serial.write(END_FLAG);
  Serial.write(0x00);
}

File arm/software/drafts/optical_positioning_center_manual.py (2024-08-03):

import time
import struct
from queue import Empty
from multiprocessing import Process, Queue

import imgui
import serial
import numpy as np
from OpenGL.GL import *

from optical_positioning import d_compute_pose as optical_pose
from optical_positioning import e_render as optical_render


class commands:
    NUL = 0x00

    SYN = 0xAB
    ACK = 0x4B
    NAK = 0x5A
    ERR = 0x3C

    RESET = 0x01
    HOME_CARRIAGE = 0x02
    HOME_SERVO = 0x03
    MOVE_CARRIAGE = 0x04
    MOVE_SERVO = 0x05


class packet_t:
    cmd = 0
    buffer = 0

    def __init__(self, buffer=b"", cmd=commands.NUL):
        self.buffer = buffer
        self.cmd = cmd


def send_packet(ser_handle, packet: packet_t):
    packet_bytes = struct.pack(
        f"<xBBB{len(packet.buffer)}sBx",
        0x7E,  # U8 start of packet flag
        packet.cmd & 0xFF,  # U8 command
        len(packet.buffer) & 0xFF,  # U8 length of payload
        packet.buffer,  # U8 payload[len]
        0x7D,  # U8 end of packet flag
    )

    ser_handle.write(packet_bytes)


def recv_packet(ser_handle):
    ser_handle.read_until(b"\x7E")

    command, length = struct.unpack("<cB", ser_handle.read(2))
    payload = b""
    if length:
        payload = struct.unpack(f"<{length}s", ser_handle.read(length))

    if ser_handle.read(1) != b"\x7D":
        print("serial frame end error")

    return packet_t(payload, ord(command))


center_find = np.array(
    [
        [-0.025, -0.06619087, +0.0105, 1.000],
        [-0.025, -0.06619087, +0.0605, 1.000],
        [+0.025, -0.06619087, +0.0605, 1.000],
        [+0.025, -0.06619087, +0.0105, 1.000],
        [0.000, 0.000, 0.000, 1.000],
    ],
    dtype=np.float32,
)


_r_circle = 0.06639085
_r_tip = 0.0285
_sample_n = 32
_sample_rad = np.linspace(0, 2 * np.pi, _sample_n)
_sample_xy = np.transpose(
    [np.cos(_sample_rad), np.sin(_sample_rad), np.ones(_sample_n)]
)
center_find_circle = _sample_xy * [_r_circle, _r_circle, +0.008]
center_find_tip = _sample_xy * [_r_tip, _r_tip, +0.00]

center_color = (0.5, 0.5, 0.5, 0.5)


def find_pose(reference_points, current_points):
    assert reference_points.shape == current_points.shape
    assert reference_points.shape[0] == 4

    centroid_ref = np.mean(reference_points, axis=0)
    centroid_cur = np.mean(current_points, axis=0)

    ref_centered = reference_points - centroid_ref
    cur_centered = current_points - centroid_cur

    H = ref_centered.T @ cur_centered
    U, _, Vt = np.linalg.svd(H)
    R = Vt.T @ U.T

    if np.linalg.det(R) < 0:
        Vt[2, :] *= -1
        R = Vt.T @ U.T

    t = centroid_cur - R @ centroid_ref

    affine_matrix = np.eye(4)
    affine_matrix[:3, :3] = R
    affine_matrix[:3, 3] = t

    return affine_matrix


def transform_points(points, transformation_matrix):
    n = points.shape[0]
    homogeneous_points = np.hstack((points, np.ones((n, 1))))

    transformed_points = transformation_matrix @ homogeneous_points.T

    transformed_points_cartesian = transformed_points[:3, :].T

    return transformed_points_cartesian


def draw_aruco_surface(markers_position):
    glEnable(GL_BLEND)
    glBlendFunc(GL_SRC_ALPHA, GL_ONE_MINUS_SRC_ALPHA)

    for marker in markers_position:
        glBegin(GL_TRIANGLE_FAN)
        glColor4f(1.0, 1.0, 1.0, 0.5)
        for point in marker:
            glVertex3f(*point @ optical_render.T)

        glEnd()


carriage_position = 0
servos_position = np.zeros(9, dtype=np.uint8)
frame_time = 0
frame_count = 0
frame_dt = 0
fps = 0


def rendering(stop_event, points_data, processing_queue):
    window = optical_render.init()
    imgui_impl = optical_render.init_imgui(window)
    imgui.style_colors_light()

    scatter = None
    while not stop_event.is_set() and not optical_render.window_should_close(window):
        while True:
            try:
                scatter = points_data.get_nowait()
            except Empty:
                break

        def draw():
            global carriage_position, servos_position, frame_time, frame_count, frame_dt, fps
            t = time.time()
            frame_dt += t - frame_time
            frame_time = t
            frame_count += 1

            if frame_count == 10:
                dt = frame_dt / 10
                fps = 1 / dt

                frame_dt = 0
                frame_count = 0

            imgui.new_frame()
            imgui.begin("controls")

            imgui.text("render")
            imgui.separator()
            imgui.text(f"fps: {fps:.4f}")

            if imgui.button("print positions"):
                print(f"servos positions: {repr(servos_position)}")
                print(f"carriage position: {repr(carriage_position)}")

            imgui.spacing()
            imgui.spacing()

            imgui.text("mechanical")
            imgui.separator()
            imgui.same_line()
            if imgui.button("home carriage"):
                processing_queue.put(packet_t(cmd=commands.HOME_CARRIAGE))
            imgui.same_line()
            if imgui.button("home servos"):
                processing_queue.put(packet_t(cmd=commands.HOME_SERVO))
            imgui.same_line()
            if imgui.button("reset"):
                processing_queue.put(packet_t(cmd=commands.RESET))

            imgui.spacing()
            imgui.spacing()

            imgui.text("servos (deg)")
            servo_changed = False
            for i, servo in enumerate(servos_position):
                if i % 3 == 0:
                    imgui.separator()
                stat, servos_position[i] = imgui.slider_int(f"{i}", servo, 0, 180)
                servo_changed |= stat
            if servo_changed:
                servo_buffer = struct.pack("<9B", *servos_position)
                packet = packet_t(buffer=servo_buffer, cmd=commands.MOVE_SERVO)
                processing_queue.put(packet)

            imgui.spacing()
            imgui.spacing()

            imgui.text("carriage (mm)")
            imgui.separator()
            carriage_changed, carriage_position = imgui.slider_float(
                "", carriage_position, 0.0, 300.0
            )
            if carriage_changed:
                steps_per_mm = 1000 / (60 * 2)
                carriage_buffer = struct.pack("<f", carriage_position * steps_per_mm)
                packet = packet_t(buffer=carriage_buffer, cmd=commands.MOVE_CARRIAGE)
                processing_queue.put(packet)

            imgui.end()

            imgui.render()
            imgui_impl.process_inputs()
            imgui_impl.render(imgui.get_draw_data())

            if scatter != None:
                markers_position, markers_map = scatter
                points = markers_position[markers_map].reshape((-1, 3))

                arm_centering_position, arm_centering_map = (
                    markers_position[8:32],
                    markers_map[8:32],
                )

                if np.sum(arm_centering_map) < 1:
                    return
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

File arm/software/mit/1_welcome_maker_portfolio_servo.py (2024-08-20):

import time

import serial
import struct


class commands:
    NUL = 0x00

    SYN = 0xAB
    ACK = 0x4B
    NAK = 0x5A
    ERR = 0x3C

    RESET = 0x01
    HOME_CARRIAGE = 0x02
    HOME_SERVO = 0x03
    MOVE_CARRIAGE = 0x04
    MOVE_SERVO = 0x05


class packet_t:
    cmd = 0
    buffer = 0

    def __init__(self, buffer=b"", cmd=commands.NUL):
        self.buffer = buffer
        self.cmd = cmd


def send_packet(ser_handle, packet: packet_t):
    packet_bytes = struct.pack(
        f"<xBBB{len(packet.buffer)}sBx",
        0x7E,  # U8 start of packet flag
        packet.cmd & 0xFF,  # U8 command
        len(packet.buffer) & 0xFF,  # U8 length of payload
        packet.buffer,  # U8 payload[len]
        0x7D,  # U8 end of packet flag
    )

    # print(packet_bytes)
    ser_handle.write(packet_bytes)


def recv_packet(ser_handle):
    ser_handle.read_until(b"\x7E")

    command, length = struct.unpack("<cB", ser_handle.read(2))
    payload = b""
    if length:
        payload = struct.unpack(f"<{length}s", ser_handle.read(length))

    if ser_handle.read(1) != b"\x7D":
        print("serial frame end error")

    return packet_t(payload, ord(command))


ser = serial.Serial(port="COM6", baudrate=115200, dsrdtr=True)

# SYN
# send_packet(ser, packet_t(cmd=commands.SYN))


def reset_servo():
    send_packet(ser, packet_t(cmd=commands.HOME_SERVO))
    print(recv_packet(ser).cmd)


def reset_carriage():
    send_packet(ser, packet_t(cmd=commands.HOME_CARRIAGE))
    print(recv_packet(ser).cmd)


def reset():
    send_packet(ser, packet_t(cmd=commands.RESET))
    print(recv_packet(ser).cmd)

    reset_carriage()
    reset_servo()


def wait_ready_move():
    while True:
        send_packet(
            ser,
            packet_t(buffer=struct.pack("<f", 0), cmd=commands.MOVE_CARRIAGE),
        )

        if recv_packet(ser).cmd == commands.ACK:
            break

        time.sleep(0.001)


def move(mm):
    steps_per_mm = 1000 / (60 * 2)
    send_packet(
        ser,
        packet_t(
            buffer=struct.pack("<f", mm * steps_per_mm), cmd=commands.MOVE_CARRIAGE
        ),
    )

    recv_packet(ser)


def s_move(deg):
    send_packet(
        ser,
        packet_t(
            buffer=struct.pack(
                "<9B",
                *np.array(deg, dtype=np.uint8),
            ),
            cmd=commands.MOVE_SERVO,
        ),
    )
    recv_packet(ser)


def s_move_interp(x1, x2, dt, steps=None):
    if steps == None:
        steps = int(dt * 32)

    dx = x2 - x1
    for i in np.linspace(0, 1, steps):
        s_move(x1 + dx * i)
        time.sleep(dt / steps)


import numpy as np


x_max = np.array([180, 0, 180, 84, 0, 180, 0, 180, 180], dtype=int)
x_min = np.array([0, 180, 132, 47, 180, 0, 180, 0, 36], dtype=int)
y_max = np.array([0, 137, 180, 0, 141, 180, 138, 168, 0], dtype=int)
y_min = np.array([180, 157, 0, 180, 107, 0, 28, 0, 180], dtype=int)
z_max = np.array([180, 180, 180, 180, 180, 180, 180, 180, 180], dtype=int)
z_min = np.zeros(9, dtype=int)

z_max_0 = np.array([180, 180, 180, 0, 0, 0, 0, 0, 0], dtype=int)
z_max_1 = np.array([180, 180, 180, 180, 180, 180, 0, 0, 0], dtype=int)

reset_servo()

dt = 0.85
input()

s_move_interp(z_min, z_max, dt)

s_move_interp(z_max, x_max, dt)
s_move_interp(x_max, y_min, dt)
s_move_interp(y_min, x_min, dt)
s_move_interp(x_min, y_max, dt)
s_move_interp(y_max, x_max, dt)
s_move_interp(x_max, z_max, dt)

s_move_interp(z_max, z_min, dt)

# input()

# x_max_0 = np.array([*x_max[0:3], *z_max[3:9]])
# x_min_0 = np.array([*x_min[0:3], *z_max[3:9]])
# y_max_0 = np.array([*y_max[0:3], *z_max[3:9]])
# y_min_0 = np.array([*y_min[0:3], *z_max[3:9]])

# dt = dt / 2

# s_move_interp(z_max, x_max_0, dt)
# s_move_interp(x_max_0, y_min_0, dt)
# s_move_interp(y_min_0, x_min_0, dt)
# s_move_interp(x_min_0, y_max_0, dt)
# s_move_interp(y_max_0, x_max_0, dt)
# s_move_interp(x_max_0, z_max, dt)

# input()
# s_move_interp(z_max, z_min, dt)

ser.close()

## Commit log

2024-06-27 flat ratio equal
    [flat_ratio_equal.scad, flat_ratio_equal.stl]
2024-06-27 flat asymmetric ratio
    [flat_asymmetric_ratio_0.5.scad, flat_asymmetric_ratio_0.5.stl, flat_asymmetric_ratio_2.scad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]
2024-06-27 flat assymetric
    [flat_asymmetric_ratio_2_8_5.scad, flat_asymmetric_ratio_2_8_5.stl]
2024-06-28 compute x offset
    [cylinder_asymmetric_ratio_2_8_5.scad]
2024-06-29 cylinder asymmetric
    [cylinder_asymmetric_ratio_2_8_5.scad]
2024-06-29 move openscad
    [cylinder_asymmetric_ratio_2_8_5.scad, flat_asymmetric_ratio_0.5.scad, flat_asymmetric_ratio_0.5.stl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]
2024-06-30 base scripts
    [flat_asymmetric_ratio_n.blend]
2024-06-30 working difference
    [flat_asymmetric_ratio_n.blend]
2024-06-30 rotate surface
    [flat_asymmetric_ratio_n.blend]
2024-06-30 rip circle
    [flat_asymmetric_ratio_n.blend]
2024-06-30 filter deletion
    [flat_asymmetric_ratio_n.blend]
2024-06-30 v1 cylinder
2024-06-30 v1 cylinder stl
    [flat_asymmetric_ratio_n_v1.stl]
2024-07-01 replace flange
    [flat_asymmetric_ratio_n.blend, flat_asymmetric_ratio_n_v2.stl]
2024-07-23 pid carriage move
2024-07-24 move servo
2024-07-25 fix timer conflict
2024-07-25 failed calibrations
2024-07-26 optimize fov, calibrate
2024-07-26 camera pointing opposite
2024-07-27 read triple camera
2024-07-29 calibrate camera
2024-07-31 detect arm tip
